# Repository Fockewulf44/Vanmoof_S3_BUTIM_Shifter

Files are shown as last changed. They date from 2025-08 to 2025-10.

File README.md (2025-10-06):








Vanmoof S3 BUTIM Shifter!
--------

Overview
--------

This is Vanmoof S3 E-shifter replacement aka **BUTIM Shifter**
</br>
I am continuously improving the mechanism.
</br>
Let me know if you have any question.
</br></br></br>

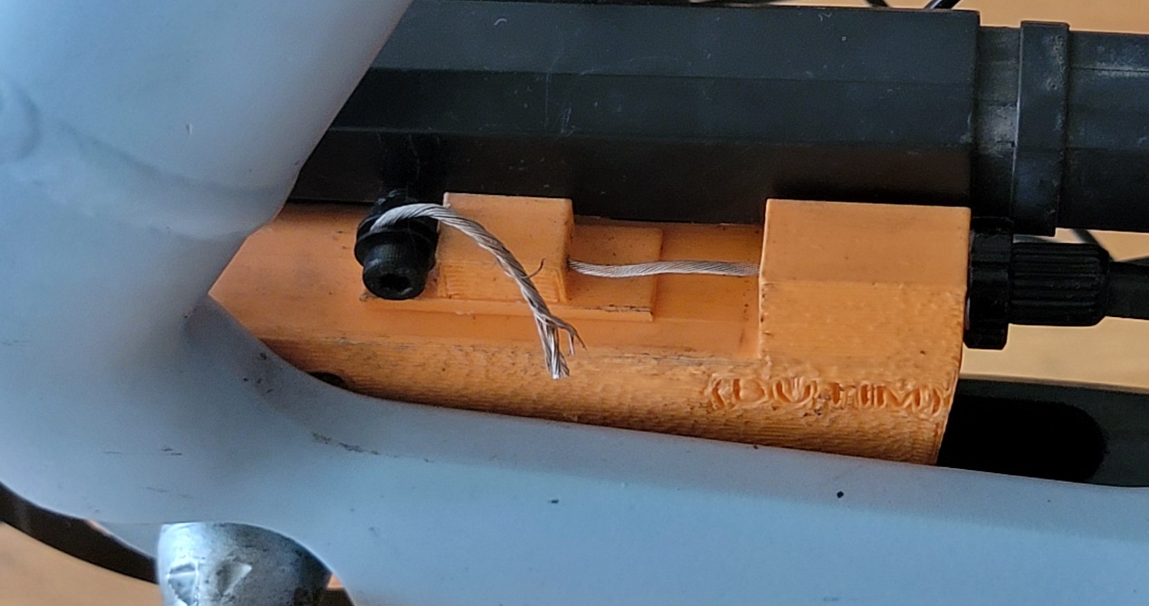
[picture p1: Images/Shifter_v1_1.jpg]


Parts you need
--------

* **3D printed parts**: Top, Bottom, Intermediate gear, Helical gear, Involute Rack(cable shifter)
  </br>
  </br>
  Printing settings:
  </br>
  Material: **PLA or PETG**
  </br>
  Infill: for Top and Bottom case **15%** or **20%**; for gears I would recommend at least **60%**;
  Involute rack **70%** and if your PLA is soft then **100%** is recommended.

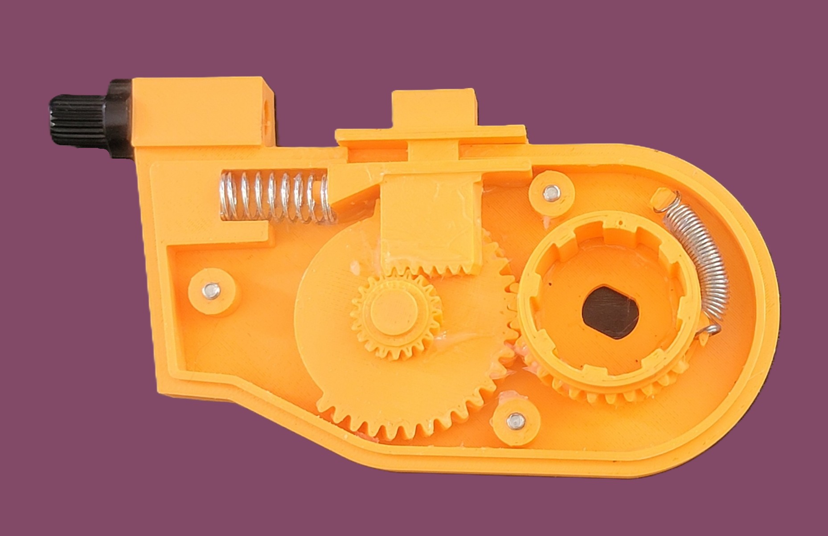
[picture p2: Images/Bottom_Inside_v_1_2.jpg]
  
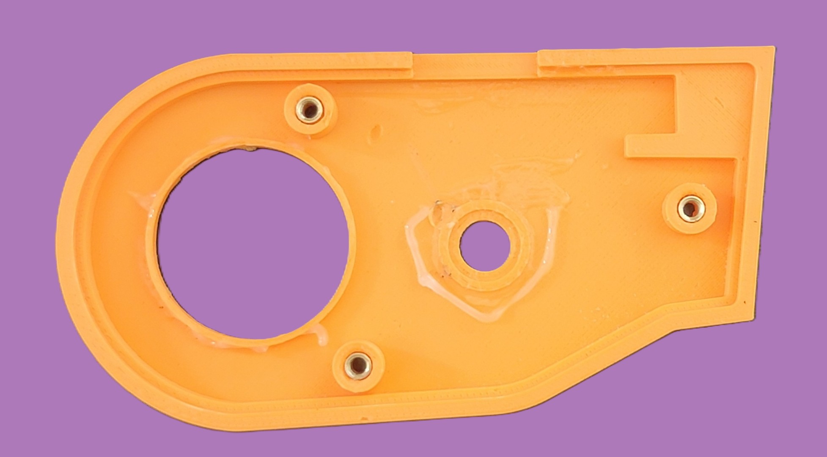
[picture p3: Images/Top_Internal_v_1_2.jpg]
  
* **Shimano Gear shifter** like 4 or 6 speed. Cable must travel **2.8mm** on each gear shift. Shimano 7 speed has a shorter cable travel, so it won't work.
  
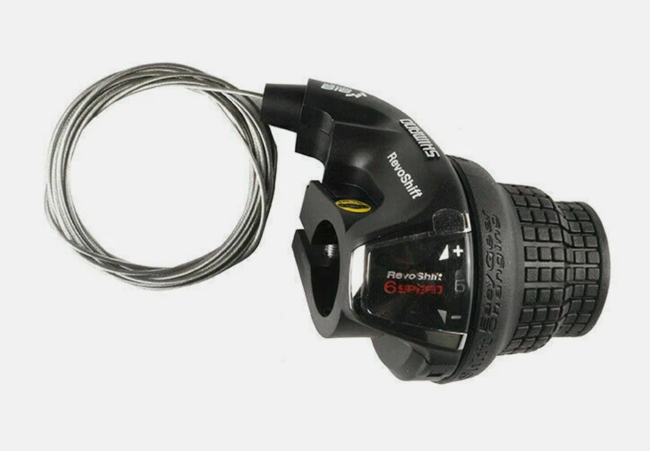
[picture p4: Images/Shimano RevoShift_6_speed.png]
  
* **M7 Brake Lever Adjuster**
  
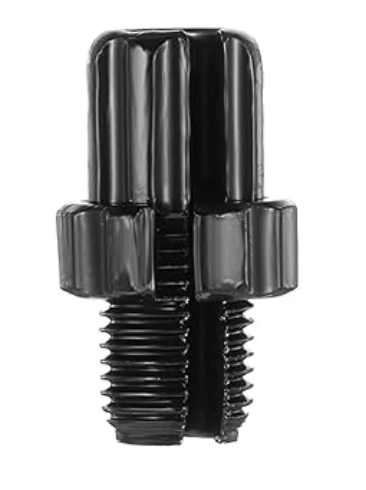
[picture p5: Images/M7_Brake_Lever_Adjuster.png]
  
* **x3 M3 heat insert nut**
* **x3 M3 screws** 20mm-25mm
* **Bike cable fixing bolt**
* **Spring** - Diameter: 9mm, Length: 3-5 cm
* **Spring** - Diameter: 4mm-6mm, Length: 2-4 cm
* **Wire Fixing Bolt**
  
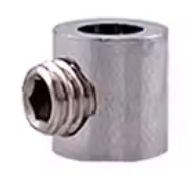
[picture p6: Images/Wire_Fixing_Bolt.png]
  
* **Silicon grease or any other plastic compatabile grease**

Assembling
----------
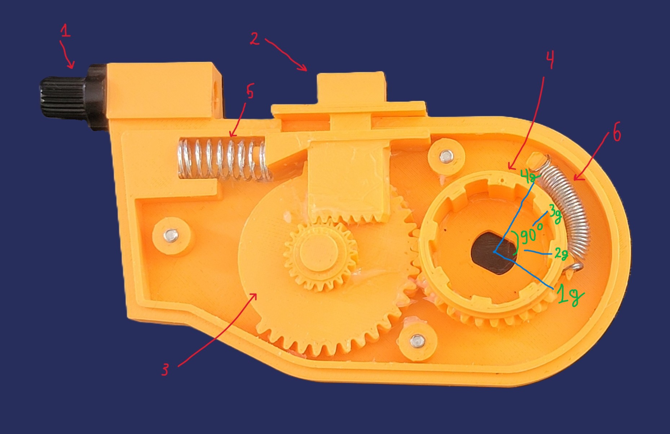
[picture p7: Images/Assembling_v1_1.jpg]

</br>

1. **M7 Brake Lever Adjuster**
2. **Cable Shifter**
3. **Intermediate gear**
4. **Helical gear**
5. **Spring with diameter 9mm**
6. **VERY VERY OPTIONAL** **Spring with diameter 5mm**

**Instruction:**
</br>
Before assembling, make sure that you put enough silicone grease. It will make shifting way smoother. After assembling add more grease.
</br>
The helical gear has a dot that indicates the current gear. Each gear corresponds to 30 degrees of rotation, so moving from first gear to fourth gear requires a total rotation of 90 degrees. Adjust Cable shifter(Involute Rack) that way that switching from first gear to fourth gear is within the range.
Shimano Revoshift needs to be cut for proper fit and not blocking a brake leverage. I used soldering iron and just melted by creating a pocket for brake leverage and it worked well.
</br>
</br>
**DON'T TIGHT THIS ONE MUCH. JUST LIGHTLY**

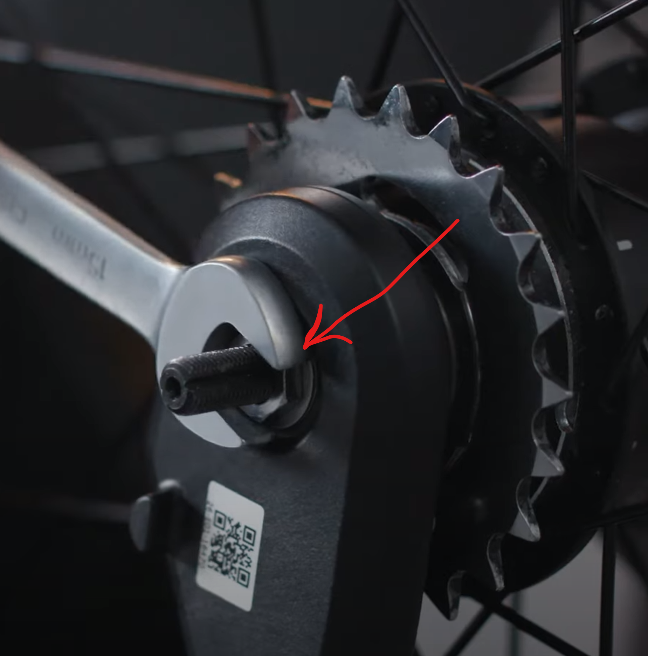
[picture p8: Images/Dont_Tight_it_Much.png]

</br></br></br>

**Enjoying this project? Buy me a coffee**
</br>



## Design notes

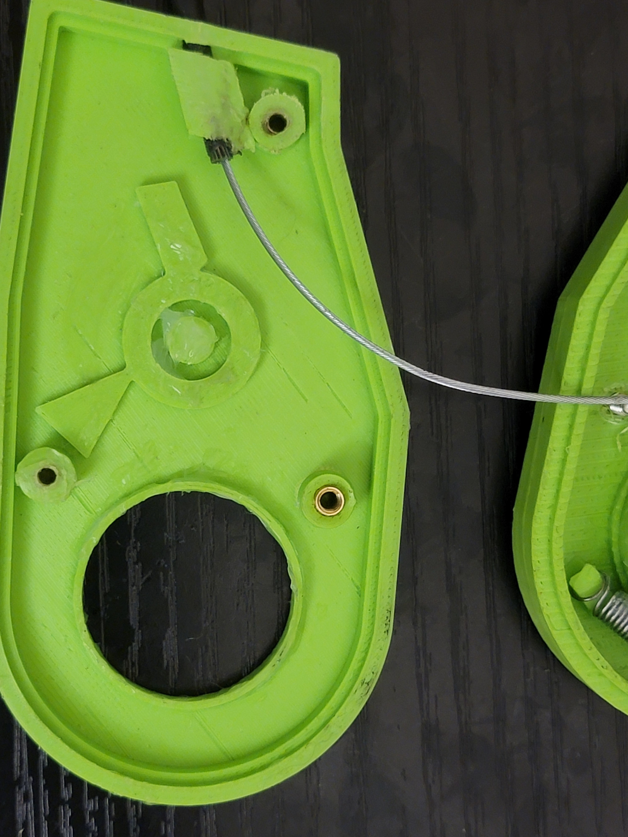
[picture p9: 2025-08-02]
Images/Top_v_1_1.jpg

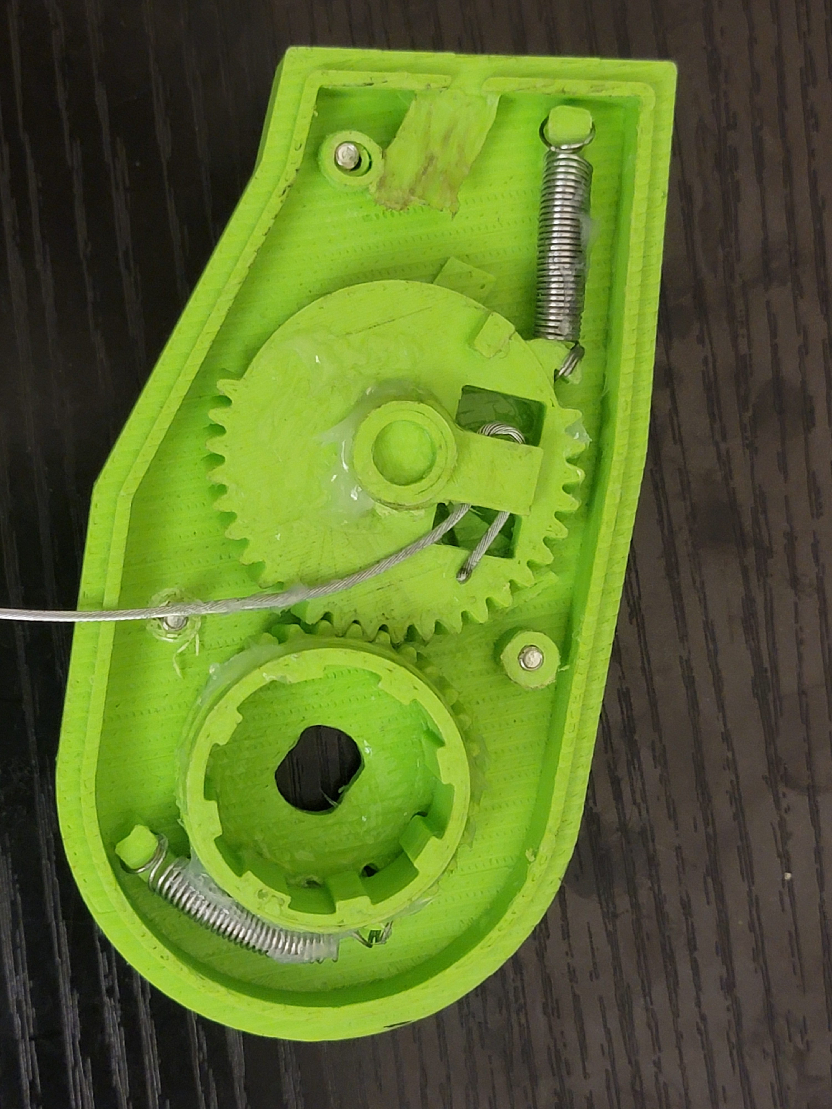
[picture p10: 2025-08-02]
Images/Bottom_v1_1.jpg

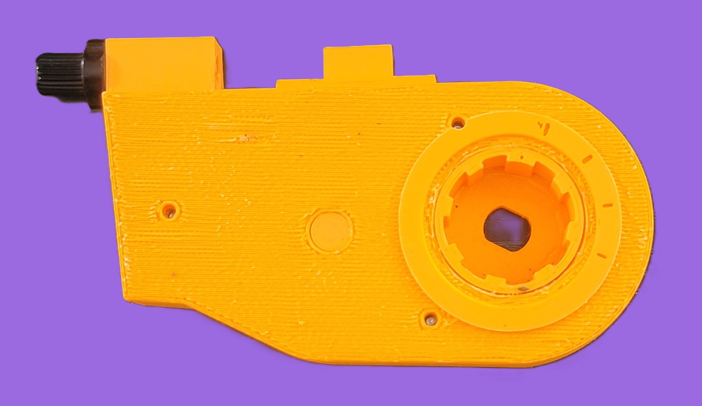
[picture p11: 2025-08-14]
Images/Top_outside_v_1_2.jpg

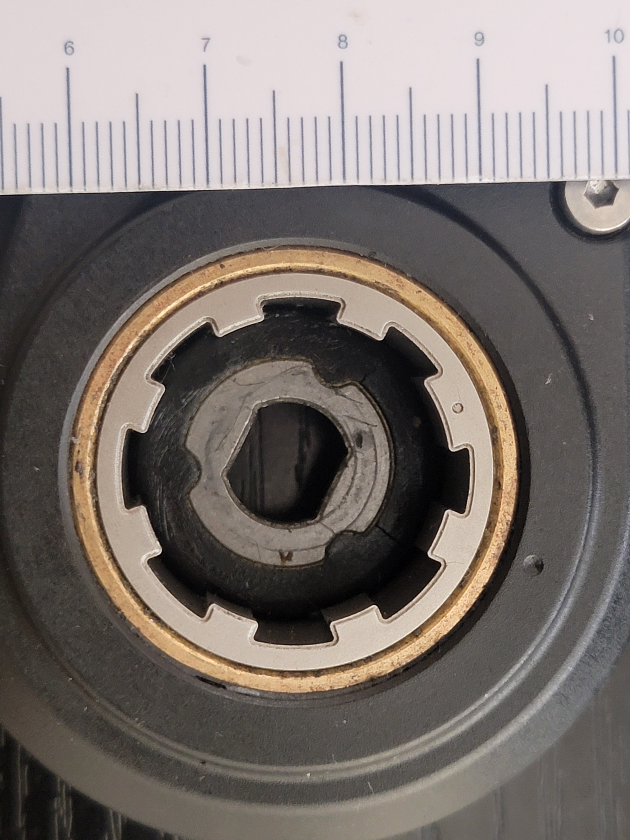
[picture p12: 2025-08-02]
Technical_pictures/M6.jpg

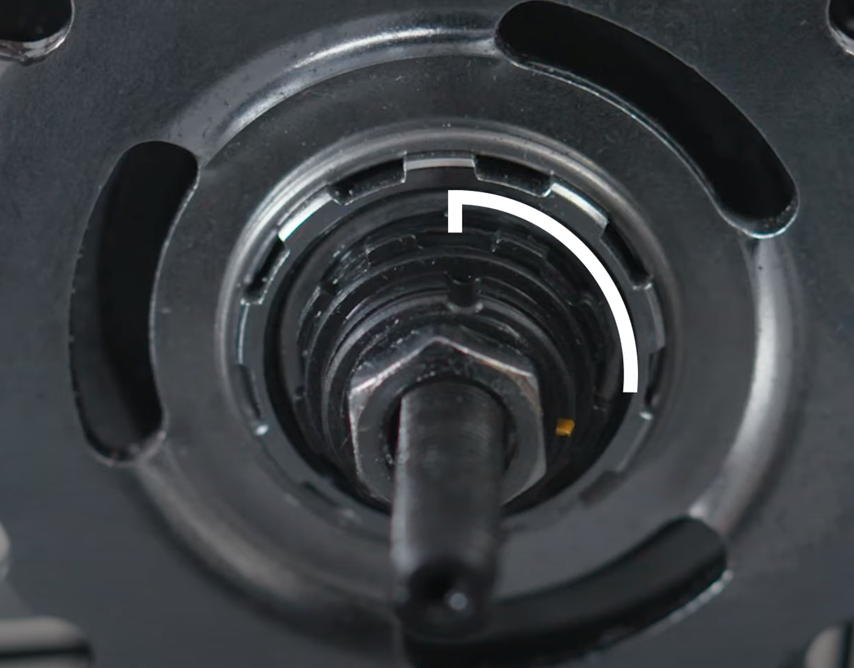
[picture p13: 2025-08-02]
Technical_pictures/90_degrees.png

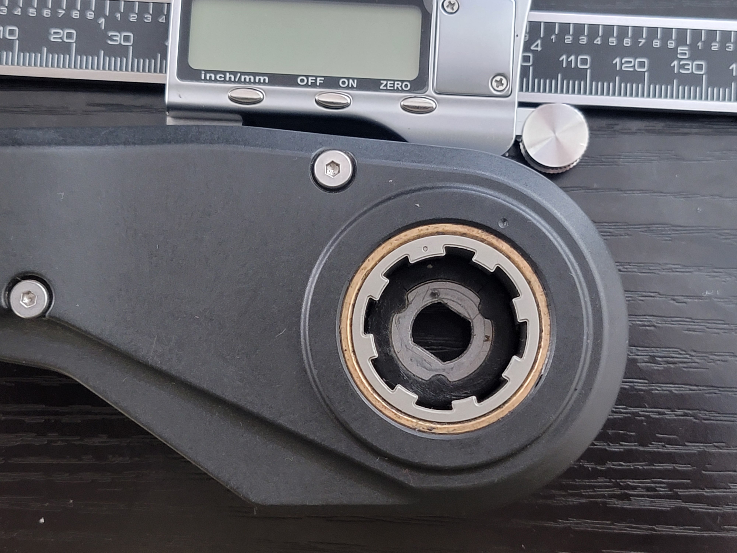
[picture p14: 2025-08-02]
Technical_pictures/M5.jpg

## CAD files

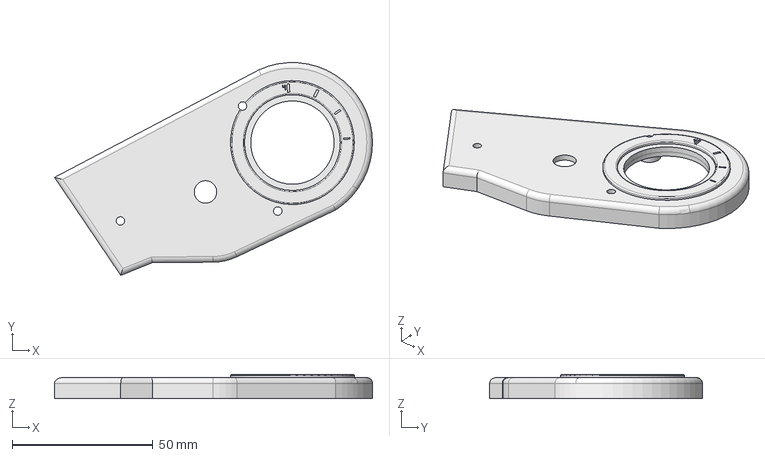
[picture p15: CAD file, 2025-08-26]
STEP/Vanmoof_ebike_shifter-Top_body.step
113.0 x 75.6 x 8.70 mm

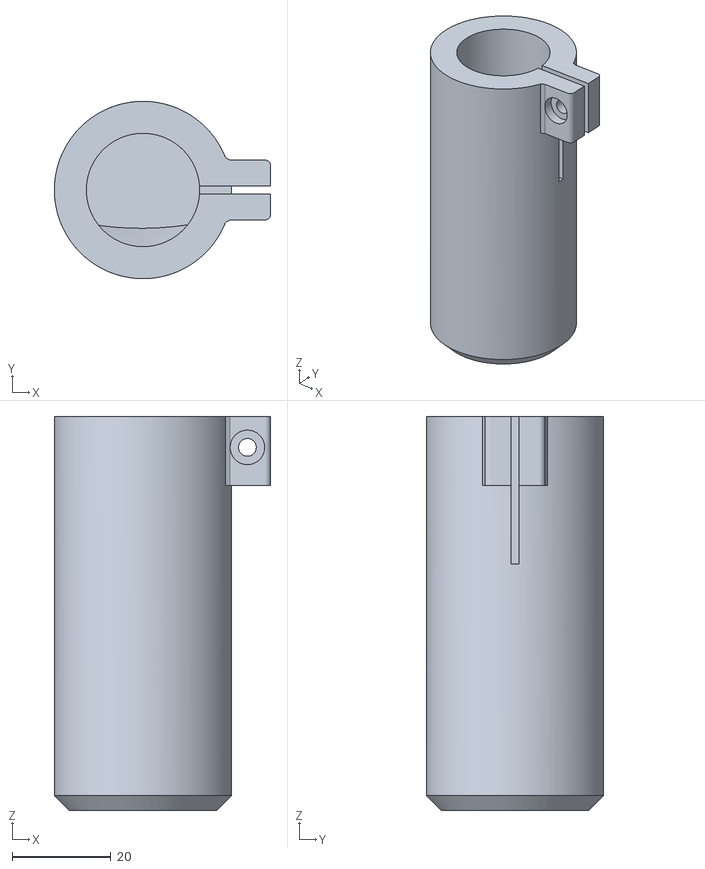
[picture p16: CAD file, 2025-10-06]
STL/Vanmoof_ebike_shifter-Handle.stl
43.9 x 36.0 x 80.0

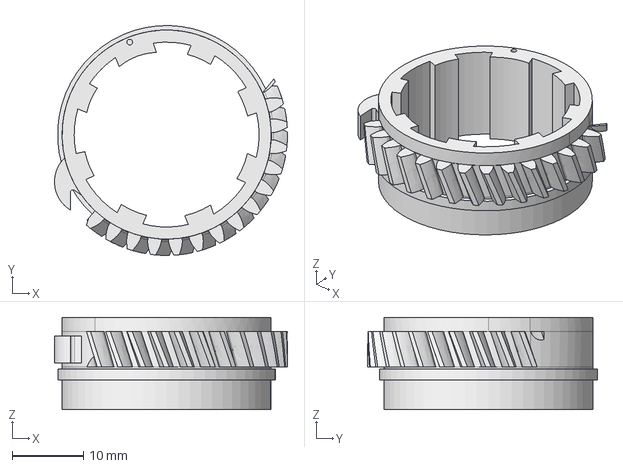
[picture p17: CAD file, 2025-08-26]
STEP/Vanmoof_ebike_shifter-Helical_gear_core.step
32.8 x 32.3 x 13.0 mm

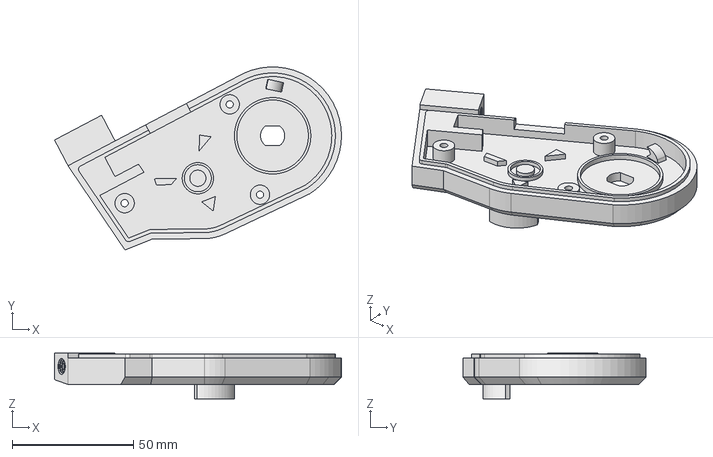
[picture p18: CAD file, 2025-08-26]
STEP/Vanmoof_ebike_shifter-Bottom_body.step
118.6 x 75.6 x 19.0 mm

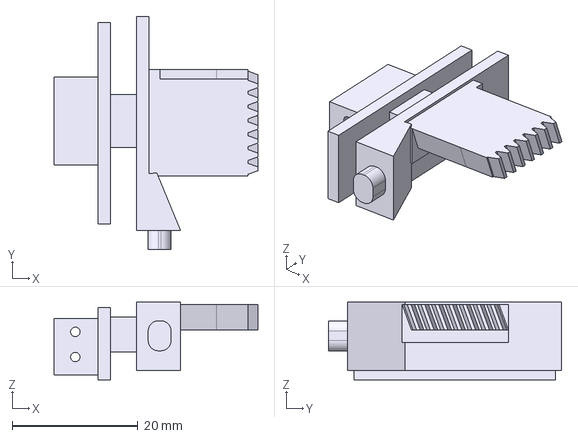
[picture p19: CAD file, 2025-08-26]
STEP/Vanmoof_ebike_shifter-Involute_Rack.step
32.4 x 37.0 x 12.4 mm

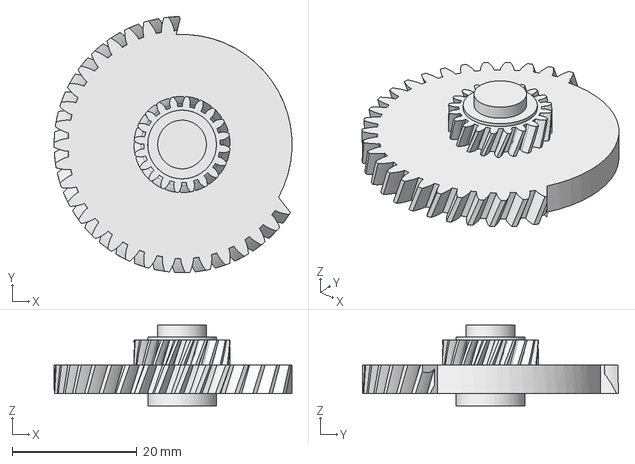
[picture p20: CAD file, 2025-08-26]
STEP/Vanmoof_ebike_shifter-Intermediate_Gear.step
38.1 x 41.0 x 12.9 mm

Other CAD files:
STL/Vanmoof_ebike_shifter-Bottom_body.stl
STL/Vanmoof_ebike_shifter-Helical_gear_core.stl
STL/Vanmoof_ebike_shifter-Intermediate_Gear.stl
STL/Vanmoof_ebike_shifter-Involute_Rack.stl
STL/Vanmoof_ebike_shifter-Top_body.stl

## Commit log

2025-08-02 Adding stls
    [Vanmoof_ebike_shifter-Bottom_body.stl, Vanmoof_ebike_shifter-Cable_Spring_Gear.stl, Vanmoof_ebike_shifter-Cable_adjuster_Internal.stl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]
2025-08-02 Reorganizing and adding some pictures
    [Vanmoof_ebike_shifter-Bottom_body.stl, Vanmoof_ebike_shifter-Cable_Spring_Gear.stl, Vanmoof_ebike_shifter-Cable_adjuster_Internal.stl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]
2025-08-07 Updated a cable gear, slowly converting it to intermediate gerar
2025-08-11 Adding cable adjuster hook
2025-08-12 Beta version
    [Vanmoof_ebike_shifter-Bottom_body.stl, Vanmoof_ebike_shifter-Cable_Spring_Gear.stl, Vanmoof_ebike_shifter-Cable_adjuster_Internal.stl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]
2025-08-14 Chambered corners, prolonged spring pocket, aded spring holder into cable hook
    [Vanmoof_ebike_shifter-Bottom_body.stl, Vanmoof_ebike_shifter-Intermediate_Gear.stl, Vanmoof_ebike_shifter-Involute_Rack.stl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]
2025-08-14 Adding m7 brake level adjuster
2025-08-14 Adding assembled on a bike pic
2025-08-14 adding assembling pic
2025-08-14 Adding some details to assembly
2025-08-23 Adding wire fixing bolt image
2025-08-23 Updating m7 brake level adjuster image
2025-08-26 Uploading step files
    [Vanmoof_ebike_shifter-Bottom_body.step, Vanmoof_ebike_shifter-Helical_gear_core.step, Vanmoof_ebike_shifter-Intermediate_Gear.step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]
2025-09-15 Update wire fixing bolt picture
2025-10-06 Modified Involute rack with adding auxillary rail and body support for stability; extended main cable hole after removing extra cable hole; added rack's rail pocket into top body.
    [Vanmoof_ebike_shifter-Bottom_body.stl, Vanmoof_ebike_shifter-Involute_Rack.stl, Vanmoof_ebike_shifter-Top_body.stl]
2025-10-06 Extended spring space; Adding handlebar grip\
    [Vanmoof_ebike_shifter-Handle.stl]
2025-10-06 Reinforced involute rack
    [Vanmoof_ebike_shifter-Involute_Rack.stl]
